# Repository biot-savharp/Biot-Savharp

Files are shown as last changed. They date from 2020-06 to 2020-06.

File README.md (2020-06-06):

# Biot-Savharp

Directory of folders/files in this repository
- ATTiny: Arduino code running on ATTiny45s (generating square waves sent to electromagnets to actuate strings)
- ArduinoISP: Arduino code to use an Arduino as an ISP to program ATTiny45s. This code is identical to the one found in the official Arduino Examples and requires some tweaking depending on what master Arduino is being used, etc.
- Datasheets: datasheets for the various chips used in the electromagnet driver board (AND gates, driver, and MOSFET)
- EM Harp: Eagle PCB layout files for the electromagnet driver board (.brd for board, .dru for design rules, .sch for schematic, and .epf for eagle project file)
- Keyboard: Arduino code running on an Arduino MEGA getting inputs from the keyboard and transmitting on/off signals for each key to the electromagnet driver board
- Keyboard_Laser: DWG file for laser-cutting the wooden keys of the keyboard
- MEGA Shield: Arduino MEGA breakout board interfacing with the keyboard and with connectors to the electromagnet driver board
- Notebook.pdf: my design notebook! The authoritative source of documentation, and a record of all the failures that led to eventual success
- harp_string_lengths.xlsx: an excel spreadsheet for calculating string lengths depending on tension

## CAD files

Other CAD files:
Keyboard_Laser/keyboard.dwg

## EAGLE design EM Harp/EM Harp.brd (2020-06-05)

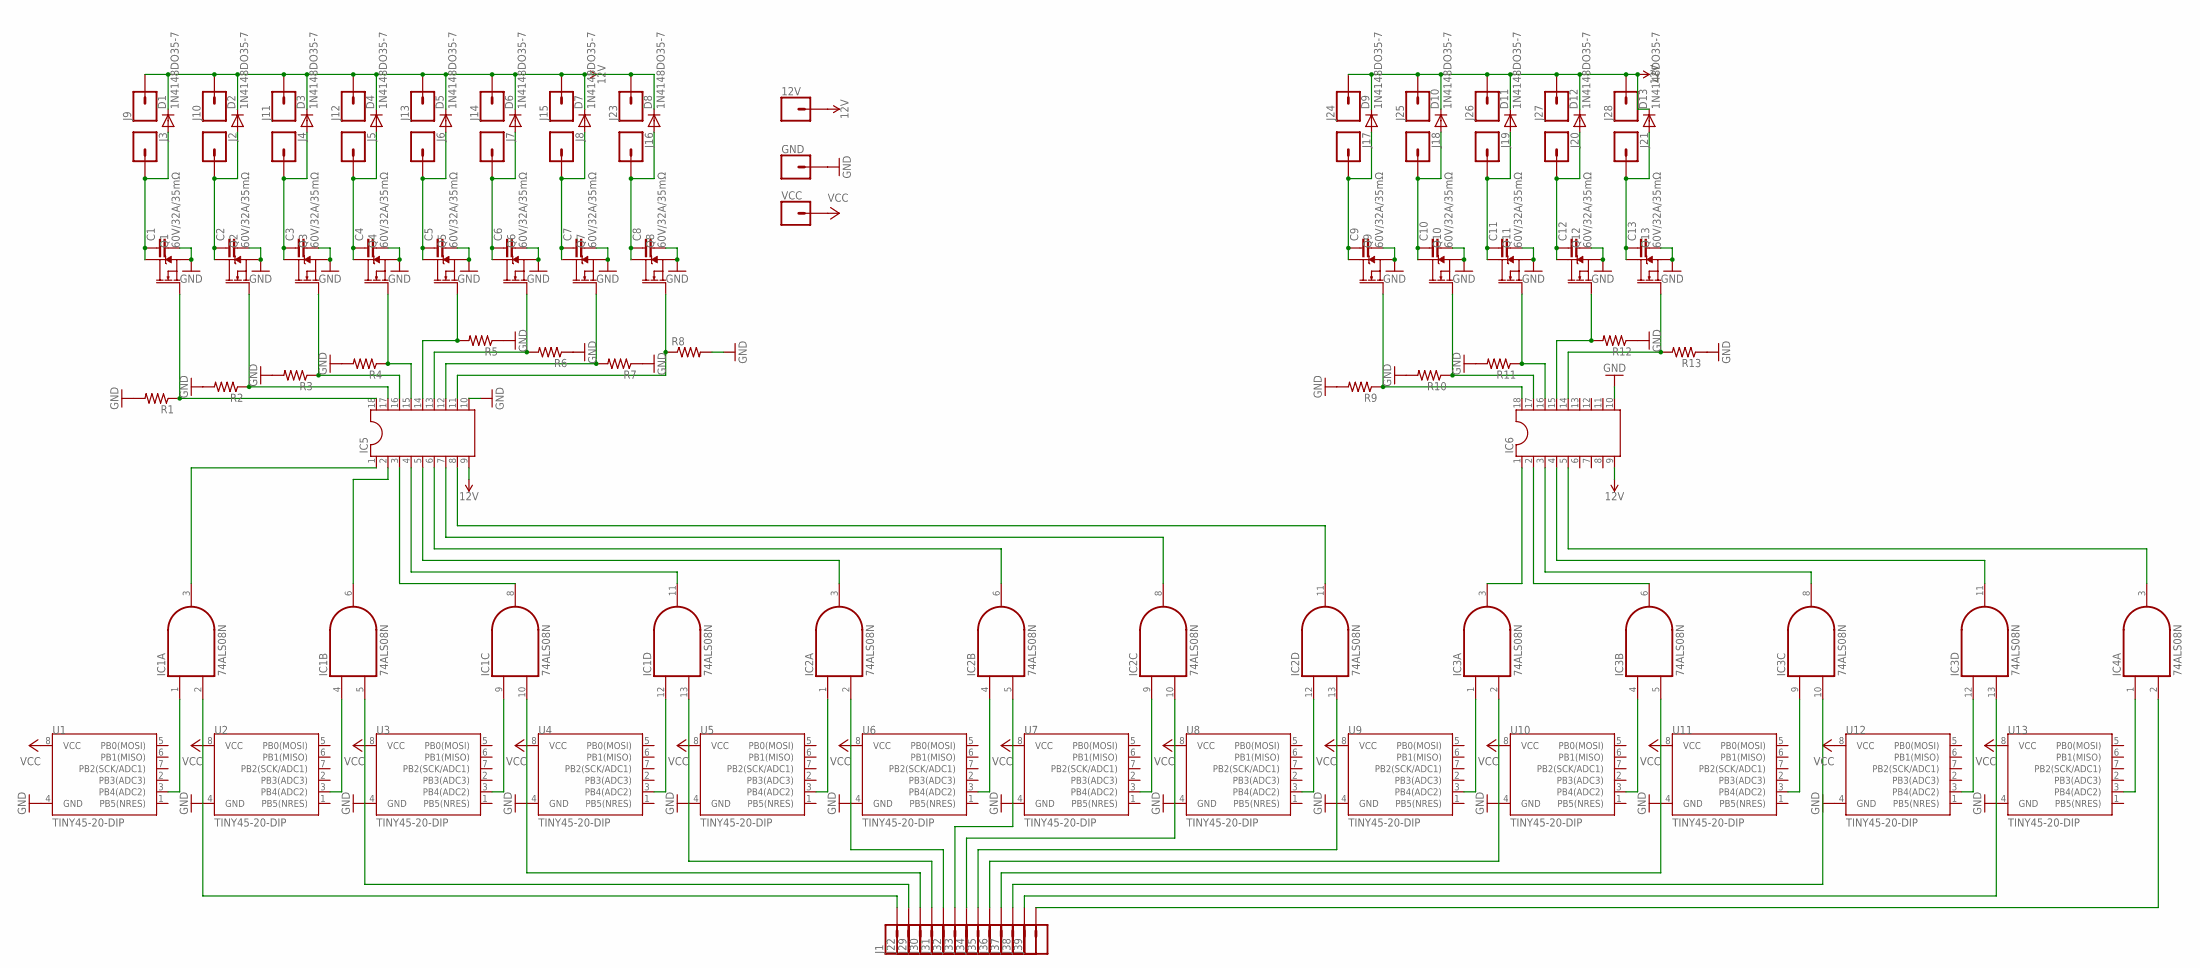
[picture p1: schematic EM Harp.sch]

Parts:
12V: CONN_01; 1X01
C1, C2, C3, C4, C5, C6, C7, C8, C9, C10, C11, C12, C13: C; C0805
D1, D2, D3, D4, D5, D6, D7, D8, D9, D10, D11, D12, D13: 1N4148DO35-7; DO35-7
GND: CONN_01; 1X01
IC1, IC2, IC3, IC4: 74ALS08N; DIL14
IC5, IC6: DIL18
J1, J2, J3, J4, J5, J6, J7, J8, J9, J10, J11, J12, J13, J14, J15, J16, J17, J18, J19, J20, J21, J22, J23, J24, J25, J26, J27, J28, J29, J30, J31, J32, J33, J34, J35, J36, J37, J38, J39: CONN_01; 1X01
Q1, Q2, Q3, Q4, Q5, Q6, Q7, Q8, Q9, Q10, Q11, Q12, Q13: 60V/32A/35mΩ; TO220V
R1: R-US_M0805; M0805
R2, R3, R4, R5, R6, R7, R8, R9, R10, R11, R12, R13: R-US_R0805; R0805
U1, U2, U3, U4, U5, U6, U7, U8, U9, U10, U11, U12, U13: TINY45-20-DIP; DIP08_MCU
VCC: CONN_01; 1X01

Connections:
12V: 12V.1, D1.C, D2.C, D3.C, D4.C, D5.C, D6.C, D7.C, D8.C, D9.C, D10.C, D11.C, D12.C, D13.C, IC5.9, IC6.9, J9.1, J10.1, J11.1, J12.1, J13.1, J14.1, J15.1, J23.1, J24.1, J25.1, J26.1, J27.1, J28.1
GND: C1.2, C2.2, C3.2, C4.2, C5.2, C6.2, C7.2, C8.2, C9.2, C10.2, C11.2, C12.2, C13.2, GND.1, IC1.7 (GND), IC2.7 (GND), IC3.7 (GND), IC4.7 (GND), IC5.10, IC6.10, Q1.3 (S), Q2.3 (S), Q3.3 (S), Q4.3 (S), Q5.3 (S), Q6.3 (S), Q7.3 (S), Q8.3 (S), Q9.3 (S), Q10.3 (S), Q11.3 (S), Q12.3 (S), Q13.3 (S), R1.2, R2.2, R3.2, R4.2, R5.1, R6.1, R7.1, R8.2, R9.2, R10.2, R11.2, R12.1, R13.1, U1.4 (GND), U2.4 (GND), U3.4 (GND), U4.4 (GND), U5.4 (GND), U6.4 (GND), U7.4 (GND), U8.4 (GND), U9.4 (GND), U10.4 (GND), U11.4 (GND), U12.4 (GND), U13.4 (GND)
unnamed: IC1.1 (I0), U1.3 (PB4(ADC2))
unnamed: IC1.4 (I0), U2.3 (PB4(ADC2))
unnamed: IC1.9 (I0), U3.3 (PB4(ADC2))
unnamed: IC1.12 (I0), U4.3 (PB4(ADC2))
unnamed: IC2.1 (I0), U5.3 (PB4(ADC2))
unnamed: IC2.4 (I0), U6.3 (PB4(ADC2))
unnamed: IC2.9 (I0), U7.3 (PB4(ADC2))
unnamed: IC2.12 (I0), U8.3 (PB4(ADC2))
unnamed: IC3.1 (I0), U9.3 (PB4(ADC2))
unnamed: IC3.4 (I0), U10.3 (PB4(ADC2))
unnamed: IC3.9 (I0), U11.3 (PB4(ADC2))
unnamed: IC3.12 (I0), U12.3 (PB4(ADC2))
unnamed: IC4.1 (I0), U13.3 (PB4(ADC2))
unnamed: IC1.2 (I1), J1.1
unnamed: IC1.5 (I1), J22.1
unnamed: IC1.10 (I1), J29.1
unnamed: IC1.13 (I1), J30.1
unnamed: IC2.2 (I1), J31.1
unnamed: IC2.5 (I1), J32.1
unnamed: IC2.10 (I1), J33.1
unnamed: IC2.13 (I1), J34.1
unnamed: IC3.2 (I1), J35.1
unnamed: IC3.5 (I1), J36.1
unnamed: IC3.10 (I1), J37.1
unnamed: IC3.13 (I1), J38.1
unnamed: IC4.2 (I1), J39.1
unnamed: IC1.3 (O), IC5.1
unnamed: IC1.6 (O), IC5.2
unnamed: IC1.8 (O), IC5.3
unnamed: IC1.11 (O), IC5.4
unnamed: IC2.3 (O), IC5.5
unnamed: IC2.6 (O), IC5.6
unnamed: IC2.8 (O), IC5.7
unnamed: IC2.11 (O), IC5.8
unnamed: IC3.3 (O), IC6.1
unnamed: IC3.6 (O), IC6.2
unnamed: IC3.8 (O), IC6.3
unnamed: IC3.11 (O), IC6.4
unnamed: IC4.3 (O), IC6.5
unnamed: IC5.18, Q1.1 (G), R1.1
unnamed: IC5.17, Q2.1 (G), R2.1
unnamed: IC5.16, Q3.1 (G), R3.1
unnamed: IC5.15, Q4.1 (G), R4.1
unnamed: IC5.14, Q5.1 (G), R5.2
unnamed: IC5.13, Q6.1 (G), R6.2
unnamed: IC5.12, Q7.1 (G), R7.2
unnamed: C1.1, D1.A, J3.1, Q1.2 (D)
unnamed: IC6.18, Q9.1 (G), R9.1
unnamed: IC6.17, Q10.1 (G), R10.1
unnamed: IC6.16, Q11.1 (G), R11.1
unnamed: IC6.15, Q12.1 (G), R12.2
unnamed: IC6.14, Q13.1 (G), R13.2
unnamed: C7.1, D7.A, J8.1, Q7.2 (D)
unnamed: C6.1, D6.A, J7.1, Q6.2 (D)
unnamed: C5.1, D5.A, J6.1, Q5.2 (D)
unnamed: C4.1, D4.A, J5.1, Q4.2 (D)
unnamed: C3.1, D3.A, J4.1, Q3.2 (D)
unnamed: C2.1, D2.A, J2.1, Q2.2 (D)
unnamed: C8.1, D8.A, J16.1, Q8.2 (D)
unnamed: C13.1, D13.A, J21.1, Q13.2 (D)
unnamed: C12.1, D12.A, J20.1, Q12.2 (D)
unnamed: C11.1, D11.A, J19.1, Q11.2 (D)
unnamed: C10.1, D10.A, J18.1, Q10.2 (D)
unnamed: C9.1, D9.A, J17.1, Q9.2 (D)
unnamed: IC5.11, Q8.1 (G), R8.1
VCC: IC1.14 (VCC), IC2.14 (VCC), IC3.14 (VCC), IC4.14 (VCC), U1.8 (VCC), U2.8 (VCC), U3.8 (VCC), U4.8 (VCC), U5.8 (VCC), U6.8 (VCC), U7.8 (VCC), U8.8 (VCC), U9.8 (VCC), U10.8 (VCC), U11.8 (VCC), U12.8 (VCC), U13.8 (VCC), VCC.1

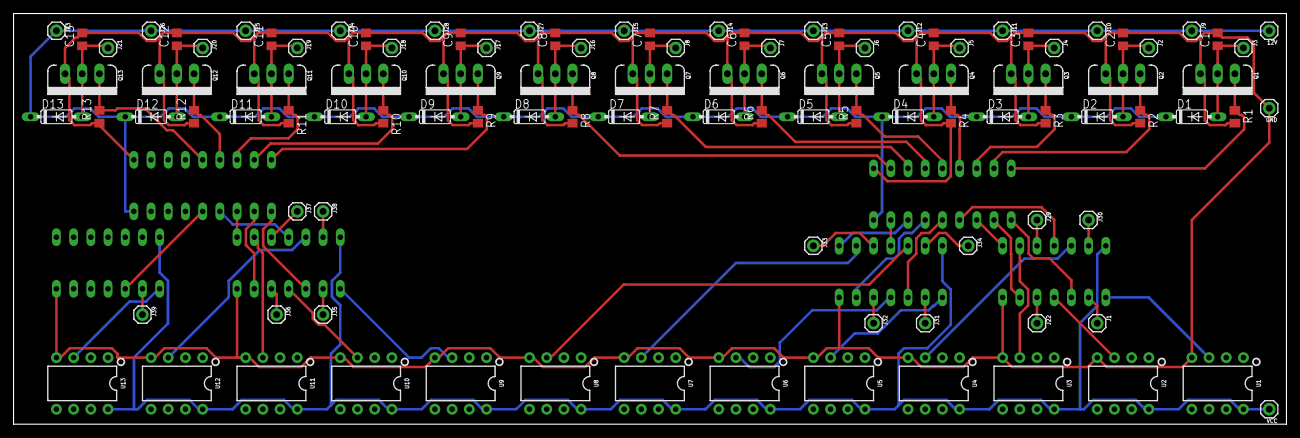
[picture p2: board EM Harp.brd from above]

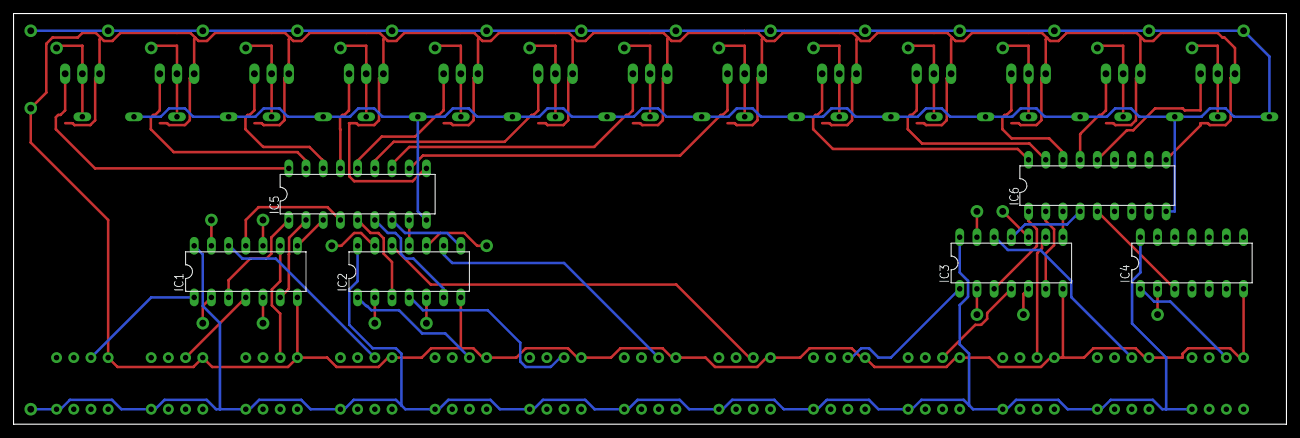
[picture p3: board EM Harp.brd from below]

Board: 2 copper layers, 187.9 x 60.6 mm, 113 parts (6 on the bottom side), 68 nets.

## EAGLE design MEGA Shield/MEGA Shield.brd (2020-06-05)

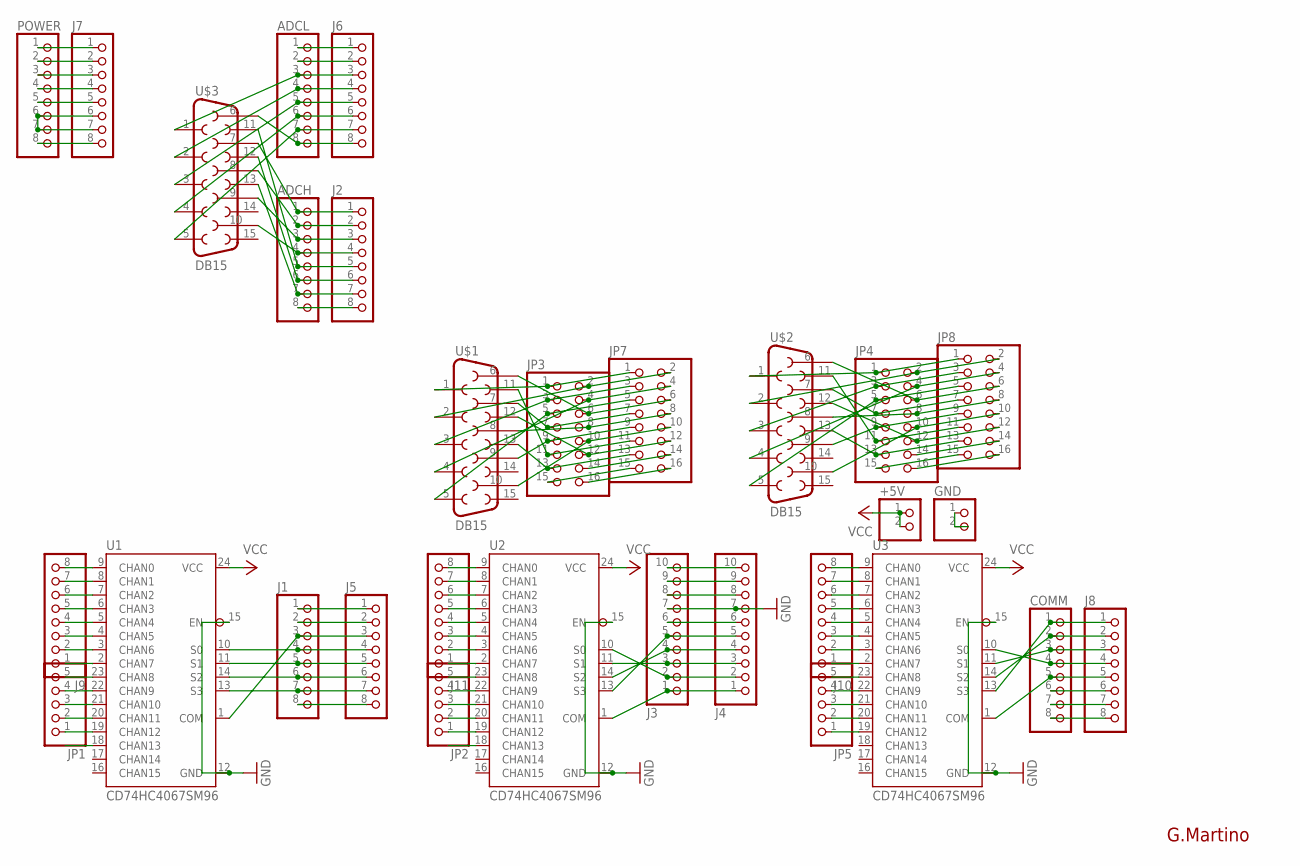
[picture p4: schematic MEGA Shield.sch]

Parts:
+5V: PINHD-1X2; 1X02
ADCH: PINHD-1X8TH; 1X08-TH
ADCL: PINHD-1X8TH; 1X08-TH
COMM: PINHD-1X8TH; 1X08-TH
GND: PINHD-1X2; 1X02
J1, J2, J5, J6, J7, J8, J9, J10, J11: PINHD-1X8TH; 1X08-TH
J3, J4: PINHD-1X10TH; 1X10-TH
JP1, JP2, JP5: PINHD-1X5; 1X05
JP3, JP4, JP7, JP8: PINHD-2X8; 2X08
POWER: PINHD-1X8TH; 1X08-TH
U1, U2, U3: CD74HC4067SM96; SSOP24
U$1, U$2, U$3: DB15

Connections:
+9V: J7.8, POWER.8
GND: J3.7, J4.7, U1.12 (GND), U1.15 (EN), U2.12 (GND), U2.15 (EN), U3.12 (GND), U3.15 (EN)
unnamed: GND.1, GND.2
unnamed: J3.1, J4.1, U2.1 (COM)
unnamed: J3.6, J4.6
unnamed: J7.5, POWER.5
unnamed: J3.4, J4.4, U2.14 (S2)
unnamed: J3.2, J4.2, U2.10 (S0)
unnamed: J3.3, J4.3, U2.11 (S1)
unnamed: J1.1, J5.1
unnamed: J1.2, J5.2
unnamed: J1.3, J5.3, U1.1 (COM)
unnamed: J1.4, J5.4, U1.10 (S0)
unnamed: J1.5, J5.5, U1.11 (S1)
unnamed: J1.6, J5.6, U1.14 (S2)
unnamed: J1.7, J5.7, U1.13 (S3)
unnamed: J1.8, J5.8
unnamed: J7.6, J7.7, POWER.6, POWER.7
unnamed: J9.8, U1.9 (CHAN0)
unnamed: ADCL.1, J6.1
unnamed: ADCL.2, J6.2
unnamed: ADCL.3, J6.3, U$3.1
unnamed: ADCL.4, J6.4, U$3.2
unnamed: ADCL.5, J6.5, U$3.3
unnamed: ADCL.6, J6.6, U$3.4
unnamed: J9.7, U1.8 (CHAN1)
unnamed: J9.6, U1.7 (CHAN2)
unnamed: J9.5, U1.6 (CHAN3)
unnamed: J9.4, U1.5 (CHAN4)
unnamed: J9.3, U1.4 (CHAN5)
unnamed: J9.2, U1.3 (CHAN6)
unnamed: J9.1, U1.2 (CHAN7)
unnamed: JP1.5, U1.23 (CHAN8)
unnamed: JP1.4, U1.22 (CHAN9)
unnamed: JP1.3, U1.21 (CHAN10)
unnamed: JP1.2, U1.20 (CHAN11)
unnamed: JP1.1, U1.19 (CHAN12)
unnamed: J10.8, U3.9 (CHAN0)
unnamed: ADCL.7, J6.7, U$3.5
unnamed: J10.7, U3.8 (CHAN1)
unnamed: J11.8, U2.9 (CHAN0)
unnamed: J11.7, U2.8 (CHAN1)
unnamed: J11.6, U2.7 (CHAN2)
unnamed: J11.5, U2.6 (CHAN3)
unnamed: J11.4, U2.5 (CHAN4)
unnamed: J11.3, U2.4 (CHAN5)
unnamed: J11.2, U2.3 (CHAN6)
unnamed: J11.1, U2.2 (CHAN7)
unnamed: JP2.5, U2.23 (CHAN8)
unnamed: JP2.4, U2.22 (CHAN9)
unnamed: JP2.3, U2.21 (CHAN10)
unnamed: JP2.2, U2.20 (CHAN11)
unnamed: JP2.1, U2.19 (CHAN12)
unnamed: J10.6, U3.7 (CHAN2)
unnamed: J10.5, U3.6 (CHAN3)
unnamed: J10.4, U3.5 (CHAN4)
unnamed: J10.3, U3.4 (CHAN5)
unnamed: J10.2, U3.3 (CHAN6)
unnamed: J10.1, U3.2 (CHAN7)
unnamed: JP5.5, U3.23 (CHAN8)
unnamed: JP5.4, U3.22 (CHAN9)
unnamed: JP5.3, U3.21 (CHAN10)
unnamed: ADCL.8, J6.8, U$3.6
unnamed: ADCH.1, J2.1, U$3.7
unnamed: JP5.2, U3.20 (CHAN11)
unnamed: JP5.1, U3.19 (CHAN12)
unnamed: ADCH.2, J2.2, U$3.8
unnamed: ADCH.3, J2.3, U$3.9
unnamed: ADCH.4, J2.4, U$3.10
unnamed: ADCH.5, J2.5, U$3.11
unnamed: ADCH.6, J2.6, U$3.12
unnamed: J7.4, POWER.4
unnamed: J3.9, J4.9
unnamed: ADCH.7, J2.7, U$3.13
unnamed: ADCH.8, J2.8
unnamed: COMM.1, J8.1, U3.13 (S3)
unnamed: COMM.2, J8.2, U3.14 (S2)
unnamed: COMM.3, J8.3, U3.11 (S1)
unnamed: COMM.4, J8.4, U3.10 (S0)
unnamed: COMM.5, J8.5, U3.1 (COM)
unnamed: COMM.6, J8.6
unnamed: COMM.7, J8.7
unnamed: COMM.8, J8.8
unnamed: J3.5, J4.5, U2.13 (S3)
unnamed: JP3.1, JP7.1, U$1.1
unnamed: JP3.2, JP7.2, U$1.2
unnamed: JP3.3, JP7.3, U$1.3
unnamed: JP3.4, JP7.4, U$1.4
unnamed: JP3.5, JP7.5, U$1.5
unnamed: JP3.6, JP7.6, U$1.6
unnamed: JP3.7, JP7.7, U$1.7
unnamed: JP3.8, JP7.8, U$1.8
unnamed: JP3.9, JP7.9, U$1.9
unnamed: JP3.10, JP7.10, U$1.10
unnamed: JP3.11, JP7.11, U$1.11
unnamed: JP3.12, JP7.12, U$1.12
unnamed: JP3.13, JP7.13, U$1.13
unnamed: JP3.14, JP7.14
unnamed: JP3.15, JP7.15
unnamed: JP3.16, JP7.16
unnamed: JP4.1, JP8.1, U$2.1
unnamed: JP4.2, JP8.2, U$2.2
unnamed: JP4.3, JP8.3, U$2.3
unnamed: JP4.4, JP8.4, U$2.4
unnamed: JP4.5, JP8.5, U$2.5
unnamed: JP4.6, JP8.6, U$2.6
unnamed: JP4.7, JP8.7, U$2.7
unnamed: JP4.8, JP8.8, U$2.8
unnamed: JP4.9, JP8.9, U$2.9
unnamed: JP4.10, JP8.10, U$2.10
unnamed: JP4.11, JP8.11, U$2.11
unnamed: JP4.12, JP8.12, U$2.12
unnamed: JP4.13, JP8.13, U$2.13
unnamed: JP4.14, JP8.14
unnamed: JP4.15, JP8.15
unnamed: JP4.16, JP8.16
unnamed: J7.2, POWER.2
unnamed: J7.1, POWER.1
unnamed: J3.8, J4.8
unnamed: J3.10, J4.10
RESET: J7.3, POWER.3
VCC: +5V.1, +5V.2, U1.24 (VCC), U2.24 (VCC), U3.24 (VCC)

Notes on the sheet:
G.Martino

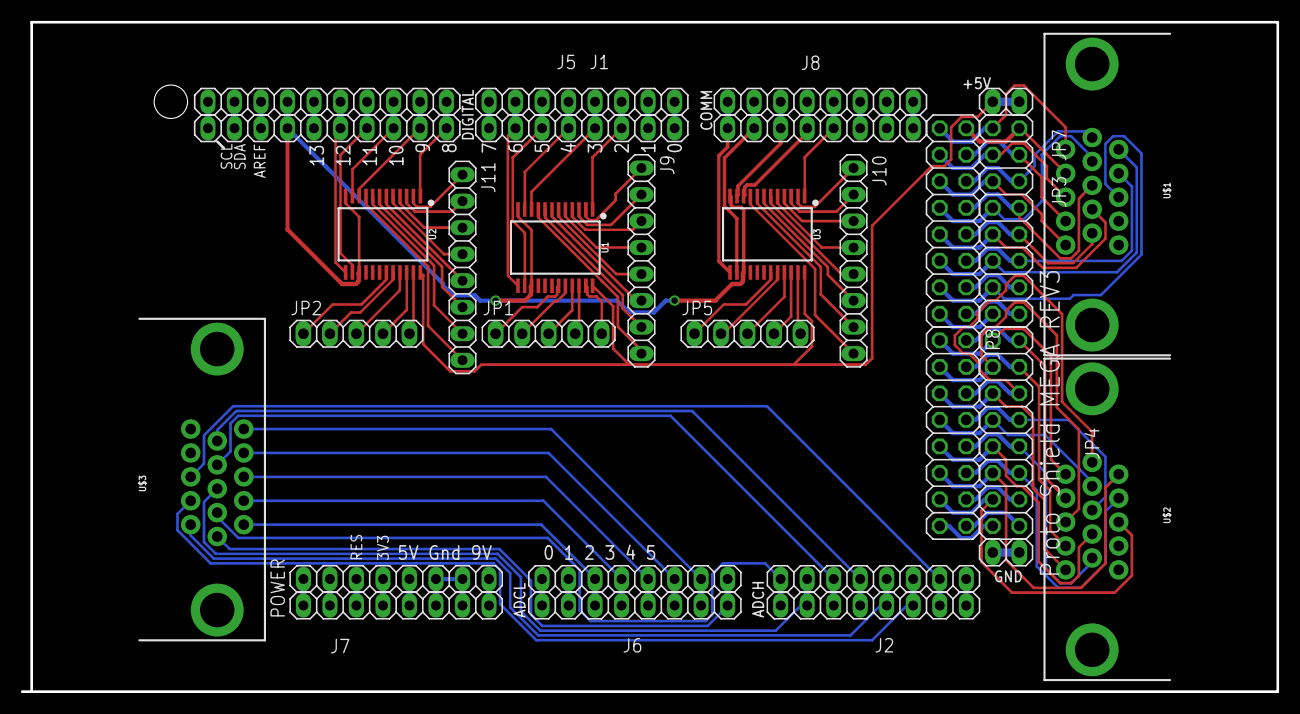
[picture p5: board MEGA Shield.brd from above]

Board: 2 copper layers, 120.3 x 64.1 mm, 30 parts (0 on the bottom side), 122 nets.

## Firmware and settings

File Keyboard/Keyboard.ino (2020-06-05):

#include "CD74HC4067.h"
#define DEBUG
//#define DEBUG2
CD74HC4067 u1(3, 4, 5, 6);
const int u1pin = 2;
CD74HC4067 u2(9, 10, 11, 12);
const int u2pin = 8;
CD74HC4067 u3(17, 16, 15, 14);
const int u3pin = 18;
#define SWITCH_PIN1 A0
#define SWITCH_PIN2 A1
static const uint8_t analog_pins[] = {A0,A1,A2,A3,A4,A5,A6,A7,A8,A9,A10,A11,A12,A13,A14};
void setup() {
  Serial.begin(9600);
  pinMode(u1pin, INPUT_PULLUP);
  pinMode(u2pin, INPUT_PULLUP);
  pinMode(u3pin, INPUT_PULLUP);
  for (int i=22; i <= 34; i++){
    pinMode(i, OUTPUT);
  }
  for (int i=38; i <= 50; i++){
    pinMode(i, OUTPUT);
  }
  for (int i=A2; i <= A14; i++){
    pinMode(i, OUTPUT);
  }
  pinMode(SWITCH_PIN1, INPUT_PULLUP);
  pinMode(SWITCH_PIN2, INPUT_PULLUP);
}
boolean switch1 = 0; //switch 1 on or off
boolean switch2 = 0; //switch 2 on or off
boolean arrHold1[39];
boolean arrHold2[39];
boolean arrTouch[39]; //touch track
boolean arrPlay[39]; //play track (logical or of hold and touch)
void loop() {
  // get pin data
  for (int i = 0; i < 13; i++) {
    u2.channel(i);
    arrTouch[i] = !digitalRead(u2pin);
  }
  for (int i = 0; i < 13; i++) {
    u1.channel(i);
    arrTouch[i + 13] = !digitalRead(u1pin);
  }
  for (int i = 0; i < 13; i++) {
    u3.channel(i);
    arrTouch[i + 26] = !digitalRead(u3pin);
  }
  // switch 1
  if (switch1 != digitalRead(SWITCH_PIN1)) { //if switch changed position
  switch1 = digitalRead(SWITCH_PIN1);
    if (switch1) { //switch went on, push to hold
      for (uint8_t i=0; i<39; i++) {
        arrHold1[i] = arrTouch[i];
      }
    } else { //switch went off, clear hold
      for (uint8_t i=0; i<39; i++) {
        arrHold1[i] = false;
      }
    }
  }
  // switch 2
  if (switch2 != digitalRead(SWITCH_PIN2)) { //if switch changed position
  switch2 = digitalRead(SWITCH_PIN2);
    if (switch2) { //switch went on, push to hold
      for (uint8_t i=0; i<39; i++) {
        arrHold2[i] = arrTouch[i];
      }
    } else { //switch went off, clear hold
      for (uint8_t i=0; i<39; i++) {
        arrHold2[i] = false;
      }
    }
  }
  //combine the two
  for (int i=0; i<39; i++) {
    arrPlay[i] = arrTouch[i] || arrHold1[i] || arrHold2[i];
  }
  Serial.print('a');
  for (int i=0; i<13; i++) {
    digitalWrite(22 + i, arrPlay[i]); //play octave 1
    #ifdef DEBUG
    Serial.print(digitalRead(22+i));
    #endif
  }
  for (int i=0; i<13; i++) {
    digitalWrite(38 + i, arrPlay[i + 13]); //play octave 1
    #ifdef DEBUG
    Serial.print(digitalRead(38+i));
    #endif
  }
  
  for (int i=0; i<13; i++) {
    digitalWrite(analog_pins[2 + i], arrPlay[i + 26]); //play octave 3
    #ifdef DEBUG
    Serial.print(digitalRead(analog_pins[2+i]));
    #endif
  }
  #ifdef DEBUG
  Serial.print('\n');
  Serial.print('b');
  for (int i = 0; i < 39; i++){
    Serial.print(arrTouch[i]);
  }
  Serial.print('\n');
  #endif
  #ifdef DEBUG2
  Serial.print(switch1);
  Serial.print(switch2);
  #endif
  delay(10);
  
}

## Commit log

2020-06-05 Add eagle files
    [EM Harp.brd, EM Harp.sch, MEGA Shield.brd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]
2020-06-05 Add arduino code
2020-06-05 Add datasheets, keyboard laser dwg, and documentation notebook
    [harp_string_lengths.xlsx, keyboard.dwg]

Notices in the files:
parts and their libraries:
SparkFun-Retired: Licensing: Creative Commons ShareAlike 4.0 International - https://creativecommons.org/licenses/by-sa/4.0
